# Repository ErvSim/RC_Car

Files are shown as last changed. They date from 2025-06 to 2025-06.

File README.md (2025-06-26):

# RC Car – Embedded Wireless Control System
## Project Overview
This project demonstrates an entry-level systems and embedded software engineering design using two Raspberry Pi Picos. One Pico reads joystick input and wirelessly transmits control signals using the nRF24L01+ radio module. The second Pico receives the data and drives a four-wheel RC car using PWM-controlled motor drivers. Designed with modularity, signal integrity, and power isolation in mind, this project integrates embedded C programming, communication protocols, real-time motor control, and low-level hardware interfaces - showcasing practical skills in both system-level planning and embedded firmware development.

## System Architecture
### TX Side (Transmitter):

- Raspberry Pi Pico reads joystick X/Y (12-bit ADC)

- Sends 4-byte payload via SPI to nRF24L01+

- Powered by 7.4V 2S LiPo → 5V buck → VSYS

### RX Side (Receiver):

- Raspberry Pi Pico receives joystick values via nRF24L01+

- Controls four TT motors via two DRV8833 motor drivers

- Separate buck converters power logic and motor subsystems

### Communication:

- nRF24L01+ (SPI-based, CE pulsed to trigger TX, RX checks STATUS)

- 4-byte payload: 2 bytes X, 2 bytes Y (scaled 12-bit ADC values)

### Components
- 2x Raspberry Pi Pico

- 2x nRF24L01+ radio modules with breakout adapters

- 4x TT gear motors (3–6V)

- 2x DRV8833 dual H-bridge motor drivers

- 2x 2S LiPo battery (7.4V nominal)

- 2x Buck converters

- 100µF electrolytic + 0.1µF ceramic capacitors (on both TX & RX)

- Joystick module (2-axis analog + button)

- 3D printed chassis (STL and SLDPRT files included)

- 2x Red LED and 1x Green LED

- 3x 330 ohm resistor

- 2x JST Plug Connector Female

- 2x 1 to 2 Splicing connectors, 2x 1 to 3 Splicing connectors

- Female to male, male to male wires

- 1x 70x90mm perfboard, 2x 20x80mm perfboard

- 10x M2 x 6mm screws

- 4x M3 x 6mm screws

- 4x M3 x 16mm screws

- 6x M3 x 30mm screws

- Pin headers

## Budget Report

| Component | Qty Used | Qty Bought | Cost Paid | Cost Used |
|---|---|---|---|---|
| Raspberry Pi Pico | 2 | 2 | $14.00 | $14.00 |
| nRF24L01+ Modules | 2 | 4 | $7.89 | $3.95 |
| nRF24L01+ Breakout Boards | 2 | 4 | $7.99 | $4.00 |
| DRV8833 Motor Drivers | 2 | 5 | $8.59 | $3.44 |
| 2S LiPo Batteries (2pack) + Charger  | 1 | 1 | $24.99 | $24.99 |
| TT Motors + Wheels (4-Pack) | 4 | 4 | $8.99 | $8.99 |
| JST Female Connectors (20AWG) | 2 | 20 | $7.19 | $0.72 |
| M3 Screws/Nuts/Washers (2240 pcs) | 14 | 2240 | $24.99 | $0.16 |
| M2 Screws (1140 pcs) | 10 | 1140 | $6.98 | $0.06 |
| 100µF + 0.1µF Capacitors | 4 | - | $0.00*** | $0.00  |
| Joystick Module | 1 | - | $0.00* | $0.00 |
| 3D Printed Chassis | 1 | - | $0.00** | $0.00 |
| LEDs + Resistors | 4 | - | $0.00*** | $0.00  |
| Splicing Connectors (1→2, 1→3) | 4 | 26 | $14.98 | $2.30 |
| Perfboards (70x90, 20x80 x2) | 3 | 32 | $6.29 | $0.59 |
| Dupont Wires (F-F, M-M) | 18 | 120 | $6.98 | $1.05 |

**Total Spent:** $139.86  
**Total Used Value in Build:** ~$64.25

\* Donated by a friend; found online for ~$6.29  
\** Printed for free at CSUN using university resources (PLA)  
\*** Already had

## Equipment Report

| Equipment | Qty Bought | Qty Used | Cost Paid | Cost Used |
|---|---|---|---|---|
| No-Clean Soldering Flux Paste (2-pack, 10CC each) | 1 | 1 | $9.99 | ~$1.50 |
| Fanttik Soldering Iron Kit | 1 | 1 | $56.20 | $56.20 |
| Kotto Fume Extractor + Helping Hands | 1 | 1 | $49.99 | $49.99 |
| 63/37 Solder Wire (100g, 0.6mm) | 1 | 1 | $7.99 | ~$2.00 |

**Total Spent on Equipment:** $124.17  
**Estimated Value Used:** ~$109.69

## Block Diagram

The following diagram illustrates the full system architecture, including the transmitter (joystick module) and receiver (RC car):

RC Car Block Diagram
*Figure: System-level block diagram showing data flow, power paths, and communication interfaces.*

## Functional Requirements
- Wireless transmission of joystick position from TX to RX

- Convert X/Y position into directional motor control

- Ensure proper power separation for logic vs motors

- Implement neutral zone and direction-switch lockout

- Maintain system stability under noisy conditions

## Interface Summary
| **Interface** | **Role** |
| :---: | :---: |
| SPI | nRF24L01+ communication |
| ADC | Read joystick values |
| GPIO | Motor control |
| PWM | Motor speed control |

## Motor Control Logic
PWM Wrap: 1561
Duty cycle calculated using:

// Forward
duty = (2000 - xvalue) / 2000.0f * 1796.0f;

// Reverse
duty = (xvalue - 2200) / (4095.0f - 2200.0f) * 1796.0f;

// 2000 and 2200 values were deadzones given for neutral based on idle joystick value readings. Due to budget-friendly motors, values are limited to max and min as gears and radio lock out and have to be power cycled.

## Direction Table
| **Action** | **X Range** | **Y Range** | **Motor Behavior** |
| :---: | :---: | :---: | :---: |
| Foward | < 100 | Neutral | All Wheels Forward |
| Reverse | > 4000 | Neutral | All wheels reverse |
| Turn Right | Neutral | < 100 | Left wheels forward, right wheels reverse |
| Turn Left | Neutral | > 4000 | Right wheels forward, left wheels reverse |
| Neutral | 500-3500 | 500-3500 | All motors stop |

## Power Design
- TX Side: 7.4V LiPo → 5V Buck → Pico (VSYS) and nRF24L01+

- RX Side:

  - Buck #1 → 5V to Pico and radio

  - Buck #2 → 5V to DRV8833 drivers

- Shared ground maintained across all components

## Troubleshooting & Debugging
Problem: RX Freeze During Non-Max and Non-Min Joystick Input
- Occurs when X is between 350-1800 and 2500-3900

- Does not occur when joystick is fully maxed or mined out (e.g., < 100 or > 4000)

- Suspected cause: current spike or transient noise interfering with SPI or the Pico

Problem: RX/TX will ACK only about 3/10 trys and locks out for a couple seconds

## Fixes Implemented
- Locked values to < 100 and > 4000 (Min and Max respectively) to make sure gears and radio never locks

- Added 100µF electrolytic and 0.1µF ceramic capacitors at power lines which increased ACK to roughly 8/10 trys but still locks out

- Isolated logic and motor power rails to make sure pico's power is steady

## Future Improvements
- Packet validation and sequence tracking
  - Make sure its a complete packet
  - The data is not corrupted
  - Verify data come from TX and not random noise

- Add display feedback or sensor integration

- Use IRQs instead of polling for RX

- Add Ultrasonic sensor for emergency stops

## Final Outcome   






## Credits & References
- Raspberry Pi Pico SDK documentation

- nRF24L01+ datasheet and communication protocols

*Special thank you to CSUN's Creator Maker Studio for allowing me to use their services free of charge, this project would have not been possible to complete without their help*

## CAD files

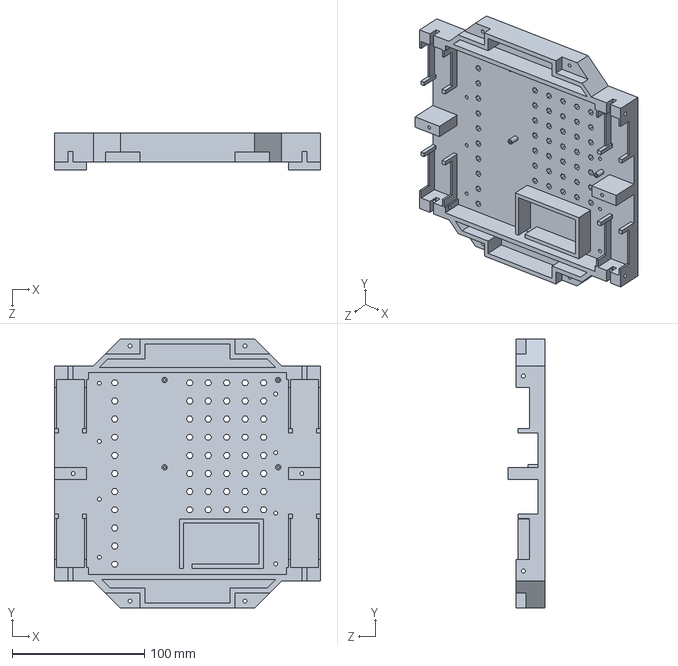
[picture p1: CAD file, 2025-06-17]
3D Prints/SLDPRT File/RC Full Base 2nd.SLDPRT
201.2 x 203.2 x 27.7 mm

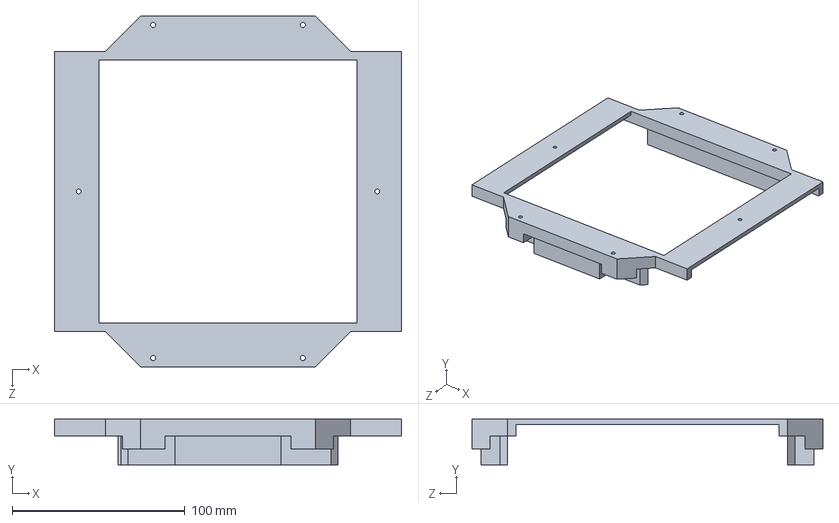
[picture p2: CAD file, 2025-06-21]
3D Prints/SLDPRT File/RC_Car_Cover.SLDPRT
201.1 x 26.5 x 203.2 mm

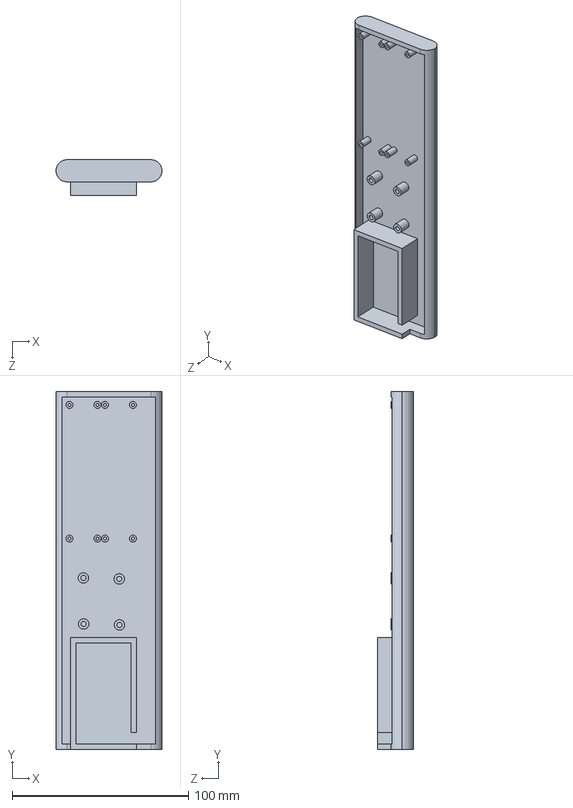
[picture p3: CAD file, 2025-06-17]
3D Prints/SLDPRT File/RC Controller.SLDPRT
60.2 x 203.2 x 20.3 mm

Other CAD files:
3D Prints/STL Files/RC Controller.STL
3D Prints/STL Files/RC Full Base 2nd.STL
3D Prints/STL Files/RC_Car_Cover.STL

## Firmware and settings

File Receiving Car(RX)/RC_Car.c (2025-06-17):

//  https://cdn.sparkfun.com/assets/3/d/8/5/1/nRF24L01P_Product_Specification_1_0.pdf   datasheet

#include <stdio.h>
#include "pico/stdlib.h"
#include "hardware/spi.h"
#include "hardware/pwm.h"
#include "NRF24L01_RX.h"
#include "PWM_Wheels.h"

// SPI Defines
// We are going to use SPI 0, and allocate it to the following GPIO pins
// Pins can be changed, see the GPIO function select table in the datasheet for information on GPIO assignments
#define SPI_PORT spi0
#define PIN_MISO 16
#define PIN_CS 17
#define PIN_SCK 18
#define PIN_MOSI 19
#define PIN_CE 20 // Chip Enable Activates RX or TX mode

#define TLRedWheel 8
#define TLBlackWheel 9
#define BLRedWheel 10
#define BLBlackWheel 11
#define TRRedWheel 12
#define TRBlackWheel 13
#define BRRedWheel 14
#define BRBlackWheel 15

void nrf_init(void);
void nrf_write_address(uint8_t reg, const uint8_t *addr, uint len);
static void read_reg(uint8_t reg, uint8_t *data, uint len);

int main()
{
    stdio_init_all();
    sleep_ms(1000);

    uint16_t xy_values[2];

    nrf_spi_init(SPI_PORT, PIN_MISO, PIN_CS, PIN_SCK, PIN_MOSI, PIN_CE);
    pwm_xy_init(TLRedWheel, TLBlackWheel);
    pwm_xy_init(BLRedWheel, BLBlackWheel);
    pwm_xy_init(TRRedWheel, TRBlackWheel);
    pwm_xy_init(BRRedWheel, BRBlackWheel);

    while (true)
    {
        if (nrf_get_adc(xy_values))
        {
            printf("→ Received X=%4u, Y=%4u\n", xy_values[0], xy_values[1]);
            set_wheel_value(
                xy_values[0],
                xy_values[1],
                TLRedWheel, TLBlackWheel,
                BLRedWheel, BLBlackWheel,
                TRRedWheel, TRBlackWheel,
                BRRedWheel, BRBlackWheel);
        }
        sleep_ms(5);
    }
}

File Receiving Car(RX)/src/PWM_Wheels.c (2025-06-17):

#include <stdio.h>
#include "pico/stdlib.h"
#include "hardware/pwm.h"

static uint TLRedWheel;
static uint TLBlackWheel;

void pwm_xy_init(uint RedWheel, uint BlackWheel)
{
    TLRedWheel = RedWheel;
    TLBlackWheel = BlackWheel;

    gpio_set_function(TLRedWheel, GPIO_FUNC_PWM);   // set to GPIO X to PWM mode
    gpio_set_function(TLBlackWheel, GPIO_FUNC_PWM); // set to GPIO Y to PWM mode

    // get slice and channel for gpio 16
    uint slice_redTLWheel = pwm_gpio_to_slice_num(TLRedWheel);
    uint channel_redTLWheel = pwm_gpio_to_channel(TLRedWheel);

    // get slice and channel for gpio17
    uint slice_blackTLWheel = pwm_gpio_to_slice_num(TLBlackWheel);
    uint channel_blackTLWheel = pwm_gpio_to_channel(TLBlackWheel);

    pwm_set_wrap(slice_redTLWheel, 1561); // got it from choosing 4.0f (random) since max of 65535 wrap got me 0.127f. Stuck with roughly 15k frequnecy
    pwm_set_wrap(slice_blackTLWheel, 1561);
    pwm_set_clkdiv(slice_redTLWheel, 4.0f); // pwm_frequency = [picos_system_clock (125M) / clkdic (4.0)] / [wrap (2082) + 1]
    pwm_set_clkdiv(slice_blackTLWheel, 4.0f);
    pwm_set_enabled(slice_redTLWheel, true); // true to enable specified pwm, false to disable it
    pwm_set_enabled(slice_blackTLWheel, true);
}

void set_wheel_value(uint16_t xvalue,
                     uint16_t yvalue,
                     uint TLRedWheel, uint TLBlackWheel,
                     uint BLRedWheel, uint BLBlackWheel,
                     uint TRRedWheel, uint TRBlackWheel,
                     uint BRRedWheel, uint BRBlackWheel)
{
    static bool must_reset_to_neutral = false;
    float duty;


    // Setup Left Wheels
    uint slice_TL_red = pwm_gpio_to_slice_num(TLRedWheel);
    uint slice_TL_black = pwm_gpio_to_slice_num(TLBlackWheel);
    uint channel_TL_red = pwm_gpio_to_channel(TLRedWheel);
    uint channel_TL_black = pwm_gpio_to_channel(TLBlackWheel);

    uint slice_BL_red = pwm_gpio_to_slice_num(BLRedWheel);
    uint slice_BL_black = pwm_gpio_to_slice_num(BLBlackWheel);
    uint channel_BL_red = pwm_gpio_to_channel(BLRedWheel);
    uint channel_BL_black = pwm_gpio_to_channel(BLBlackWheel);

    // Setup Right Wheels
    uint slice_TR_red = pwm_gpio_to_slice_num(TRRedWheel);
    uint slice_TR_black = pwm_gpio_to_slice_num(TRBlackWheel);
    uint channel_TR_red = pwm_gpio_to_channel(TRRedWheel);
    uint channel_TR_black = pwm_gpio_to_channel(TRBlackWheel);

    uint slice_BR_red = pwm_gpio_to_slice_num(BRRedWheel);
    uint slice_BR_black = pwm_gpio_to_slice_num(BRBlackWheel);
    uint channel_BR_red = pwm_gpio_to_channel(BRRedWheel);
    uint channel_BR_black = pwm_gpio_to_channel(BRBlackWheel);

    bool is_neutral = (xvalue > 500 && xvalue < 3500) && (yvalue > 500 && yvalue < 3500);

    if (is_neutral)
    {
        // Reset all motors
        pwm_set_chan_level(slice_TL_red, channel_TL_red, 0);
        pwm_set_chan_level(slice_TL_black, channel_TL_black, 0);
        pwm_set_chan_level(slice_BL_red, channel_BL_red, 0);
        pwm_set_chan_level(slice_BL_black, channel_BL_black, 0);
        pwm_set_chan_level(slice_TR_red, channel_TR_red, 0);
        pwm_set_chan_level(slice_TR_black, channel_TR_black, 0);
        pwm_set_chan_level(slice_BR_red, channel_BR_red, 0);
        pwm_set_chan_level(slice_BR_black, channel_BR_black, 0);
        must_reset_to_neutral = false;
    }
    else if (!must_reset_to_neutral)
    {
        // Forward
        if (xvalue < 100 && (yvalue > 500 && yvalue < 3500))
        {
            duty = (2000 - xvalue) / 2000.0f * 1796.0f;

            // All wheels forward
            pwm_set_chan_level(slice_TL_red, channel_TL_red, duty);//Left Side
            pwm_set_chan_level(slice_TL_black, channel_TL_black, 0);
            pwm_set_chan_level(slice_BL_red, channel_BL_red, duty);
            pwm_set_chan_level(slice_BL_black, channel_BL_black, 0);

            pwm_set_chan_level(slice_TR_red, channel_TR_red, 0);//Right Side
            pwm_set_chan_level(slice_TR_black, channel_TR_black, duty);
            pwm_set_chan_level(slice_BR_red, channel_BR_red, 0);
            pwm_set_chan_level(slice_BR_black, channel_BR_black, duty);

            must_reset_to_neutral = true;
        }
        // Reverse
        else if (xvalue > 4000 && (yvalue > 500 && yvalue < 3500))
        {
            duty = (xvalue - 2200) / (4095.0f - 2200.0f) * 1796.0f;

            // All wheels reverse
            pwm_set_chan_level(slice_TL_red, channel_TL_red, 0);        //Left Side
            pwm_set_chan_level(slice_TL_black, channel_TL_black, duty);
            pwm_set_chan_level(slice_BL_red, channel_BL_red, 0);
            pwm_set_chan_level(slice_BL_black, channel_BL_black, duty);

            pwm_set_chan_level(slice_TR_red, channel_TR_red, duty);        //Right Side
            pwm_set_chan_level(slice_TR_black, channel_TR_black, 0);
            pwm_set_chan_level(slice_BR_red, channel_BR_red, duty);
            pwm_set_chan_level(slice_BR_black, channel_BR_black, 0);

            must_reset_to_neutral = true;
        }
        // Right Turn: left wheels forward, right wheels reverse
        else if (yvalue < 100 && (xvalue > 500 && xvalue < 3500))
        {
            duty = (2000 - yvalue) / 2000.0f * 1796.0f;

            pwm_set_chan_level(slice_TL_red, channel_TL_red, duty);    //Left Side
            pwm_set_chan_level(slice_TL_black, channel_TL_black, 0);
            pwm_set_chan_level(slice_BL_red, channel_BL_red, duty);
            pwm_set_chan_level(slice_BL_black, channel_BL_black, 0);

            pwm_set_chan_level(slice_TR_red, channel_TR_red, duty);        //Right Side
            pwm_set_chan_level(slice_TR_black, channel_TR_black, 0);
            pwm_set_chan_level(slice_BR_red, channel_BR_red, duty);
            pwm_set_chan_level(slice_BR_black, channel_BR_black, 0);

            must_reset_to_neutral = true;
        }
        // Left Turn: left wheels reverse, right wheels forward
        else if (yvalue > 4000 && (xvalue > 500 && xvalue < 3500))
        {
            duty = (yvalue - 2200) / (4095.0f - 2200.0f) * 1796.0f;

            pwm_set_chan_level(slice_TL_red, channel_TL_red, 0);        //Left Side
            pwm_set_chan_level(slice_TL_black, channel_TL_black, duty);
            pwm_set_chan_level(slice_BL_red, channel_BL_red, 0);
            pwm_set_chan_level(slice_BL_black, channel_BL_black, duty);

            pwm_set_chan_level(slice_TR_red, channel_TR_red, 0);     //Right Side
            pwm_set_chan_level(slice_TR_black, channel_TR_black, duty);
            pwm_set_chan_level(slice_BR_red, channel_BR_red, 0);
            pwm_set_chan_level(slice_BR_black, channel_BR_black, duty);

            must_reset_to_neutral = true;
        }
    }
}
